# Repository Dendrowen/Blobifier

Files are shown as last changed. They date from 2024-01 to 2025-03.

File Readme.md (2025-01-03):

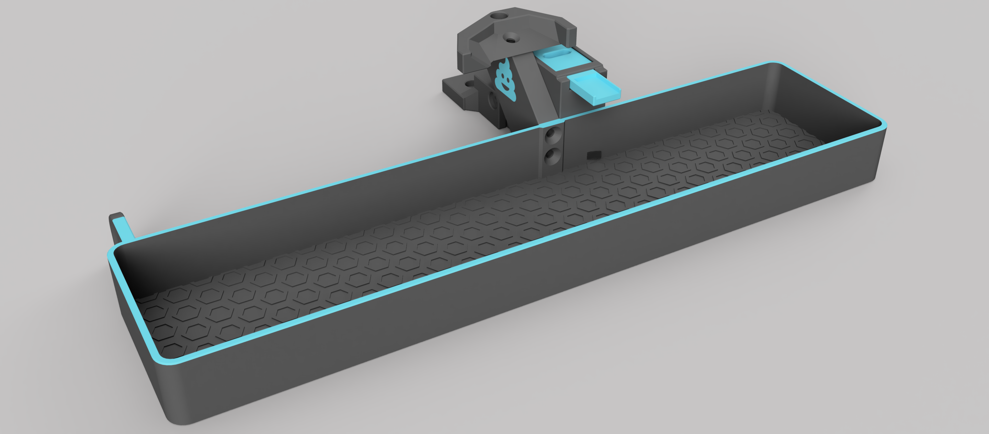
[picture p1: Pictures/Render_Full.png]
Blobifier Render

Do you like the Blobifier? Consider [buying me a coffee](https://www.buymeacoffee.com/dendrowen) or support me through [paypal](https://www.paypal.com/donate/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)

# 1. What is it?
The Blobifier is a small device that eliminates the need for a purgeblock, making filament swaps more quick. It does this by extruding filament onto a tray creating a blob that will get ejected into a purge-bucket.
## 1.1 Features
- Turn your filament purge waste into blobs for fewer waste and quicker purging.
- Store the blobs in a bucket that can hold **400 blobs!** (for the V2 300mm version)
- Automatically pause the printer once the bucket is full.
- Detect when the bucket is installed or missing.
    - NOTE: Empty the bucket if you remove it! The system will reset the blob counter.
- Shake the bucket for better dispersion of the blobs in the bucket.
- Clean your nozzle on a brass brush before resuming to print.

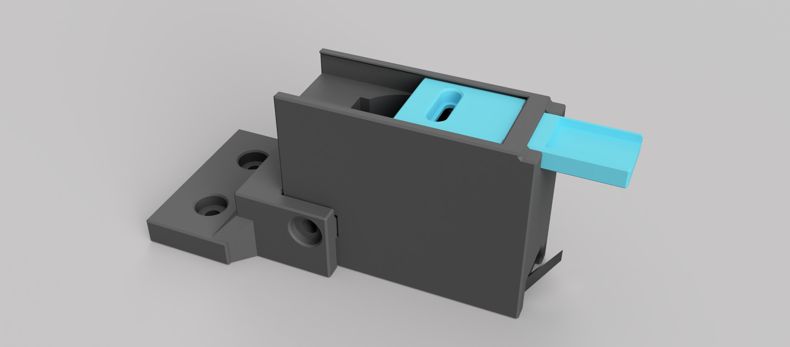
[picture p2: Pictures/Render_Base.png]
Blobifier Render


Blobifier Video (https://www.youtube.com/watch?v=VNMafOdnZ84) Blobifier Video (https://www.youtube.com/watch?v=a73EYLjRkbQ)

# 2. Credit where credit is due
The Macro and Nozzle Scrubber are based on a version madde by by Hernsl (hernsl#8860 on Discord). 

# 3. Who is it for?
The device is designed around a Voron V2.4 300mm, but should work for 250mm and 350mm too. This version only supports the assembly on the rear-left of the bed. If you decide to change all this, please consider contributing to the project by creating a pull request with the needed changes.

# 4. BOM
Complete kit at:
- [aliexpress - Seleadlab](https://s.click.aliexpress.com/e/_DCsTsHL)
- [aliexpress - Fysect](https://s.click.aliexpress.com/e/_opb6U3d)
    - Requires other .stl files. Linked in the product description!
- .stl files should be printed using default Voron settings
  
Parts:
- 3 x M3x8 shsc
- 1 x M3x25 shsc
- 3 x M3x8 fhcs
- 3 x M3 t-nut
- 1 x M2x6 shsc (For the servo pivot arm)
- 2 x M2x10 self tapping screws
- 5 x heat set inserts
- 1 x 10x30 aluminum strip
    - max 1mm thick
    - Make sure it's thick enough to dissipate the heat from the nozzle
    - If you have the 'old' 10x15 strip, print the proper tray to match it.
- 1 x SG90 or MG90 servo (and the included screws)
- 1 x omron D2F-5L sized micro switch. Any knock-off will work.
- 1 x brass brush
- 1 x 4-pin jst connector set (male + female)
- other connectors and wire to connect it to the board

# 5. Build instructions
## 5.1 Bucket
### 5.1.1 Printed Parts
- **Bucket_*.stl** (whichever suits your printer (and printbed))
- **\*_Shaker.stl** (whichever suits your toolhead)
- **\*_Shaker_Arm.stl** (whichever suits your toolhead)
    - The included **\*_Shaker_arm_poo.stl** can be used for a multimaterial print.
### 5.1.2 Assembly
1. Insert 4 heatset inserts in the arm. Mind that one needs to be inserted at an angle.
2. Screw the arm to the bucket with the *poo* being upright using 2 M3x8 fhcs screws.
3. Screw the shaker to the arm with the opening facing the bucket using an M3x8 fhcs and M3x8 shsc screw.

## 5.2 Brush
### 5.2.1 Printed Parts
- **Brush.stl**
### 5.2.2 Assembly
1. Cut off the handle from the brass brush and insert it into the printed part. If it doesn't fit smootly, file down the brush further until it does.
2. Screw the brush down on the left bed extrusion with the brush against the rear of the bed using an M3x8 shcs and t-nut.

## 5.3 Base
### 5.3.1 Printed Parts 
- **Base.stl**
- **Tray.stl**
- **Servo_arm_*.stl** (Check which arm fits properly on your servo)
- **Mount_*.stl** Check the mount for your printer. The V2.4 has two mounts because some beds are slightly wider(255, 305 or 355)
- **Base_shim.stl** The tray needs to be sligtly above the bed surface (Scale Z height of the object according to your needs. Keep in mind that the higher this part is, the longer the mounting screws need to be)
### 5.3.2 Assembly
1. Glue the piece of aluminum inside the tray. It might require a little force to make it slide into the cavity. Make sure the piece of aluminum is thick enough to dissipate heat from the nozzle without melting the plastic.
1. Sand down the tray untill the top and bottom are smooth. If the aluminum pertrudes the top a bit, sand that down with it.
1. Remove 3 included support from the base.
    - One in the slot for the tray
    - Two at the bottom for the switch and jst connector
1. Test fit the tray in the base. Slide it in from the back. It should stick out 15mm if fully inserted. If operation isn't smooth, go back to step 2.
1. Remove the tray from the base
1. Insert the servo from above making sure the wires face the cavity meant for them and are inserted first so they come out from the bottom. It could be a tight fit, but if your printer is properly tuned you shouldn't have any trouble. Make sure you inserted it fully, you can check from the bottom.
1. Insert the microswitch in the bottom. Check if the lever is correctly oriented. Screw it down with 2 M2x10 self tapping screws. The screw holes might be hard to see, because there is an extra layer for printability.
1. Insert the 4-pin female JST connector iside the slot. If the fit is very loose, use some glue. 
1. Solder the wires from the servo and the switch to this connector. The order is less important, just keep in mind that you'll have to connect the wire to the board in the same order.
    - pin 1: VCC (Red, usually)
    - pin 2: 
        - GND from the servo (Brown, usually)
        - C from the switch (pins are marked C, NC and NO)
    - pin 3: Signal wire from servo (Orange, usually)
    - pin 4: NC from the switch
1. Connect the base to your printer with a cable of your own making. You can drill a hole in the bottom plate of your printer to feed the wire through. **Be careful not to hit any components in your electronics compartment and ALWAYS unplug your printer from the wall if you're working on the electronics!** You'll have to pick empty pins on your board. Refer to your boards documentation on which pins to use.
    - pin 1: 5V (any 5V on your board should work)
    - pin 2: GND (any GND on your board should work)
    - pin 3: An output capable pin. Most of them are.
    - pin 4: A pin with an internal pullup resistor. Most of them have.
1. Insert a heated insert into the base mount. Only one side is suitable for it.
1. Slide the base in the mount and secure it with an M3x25 shsc.
1. Screw the base into place with 2 x M3x8 shcs and T-nuts onto the left 2020 extrusion. The tray should just slide behind your bed. You can temporarily insert the tray to verify the position.
1. Turn on your printer and include the config file found in the github. Then restart the klipper firmware.
1. run `BLOBIFIER_SERVO POS=out` in the console. You should hear your servo move.
1. Screw the servo arm onto the servo with the arm pointing towards the slot. Make sure you don't turn the servo while doing this. If you accidentally turn it, run `BLOBIFIER_SERVO POS=out` again and continue.
1. Insert the tray from the back until the hole in the servo arm becomes visible through the tray. Then screw it down with an M2x4 screw, then go back half a turn so the screw can rotate freely in the tray.
1. Test the servo a couple of times with `BLOBIFIER_SERVO POS=in` and `BLOBIFIER_SERVO POS=out`. The tray should be fully inside or outside the base. If not, try to determine why.
    - There may be too much resistance in the sliding mechanism.
    - You might have screwed the m2 screw too tight.
    - The values in the config might need adjustment (unlikely)
1. Push the switch on the base. A message that the bucket is placed should be on the screen. Then let go of the switch. A message that the bucket was removed should be on the screen.
1. Place the bucket and see if it still works. If not, the base might need slight adjustment towards the center.

# 6. Configuration
Refer to the config files comments to configure the macro to your desires.

For maximum integration with Happy Hare, make use of the [gcode pre-processing](https://github.com/moggieuk/Happy-Hare/wiki/Gcode-Preprocessing). Make sure to include `PURGE_VOLUMES=!purge_volumes!`

Add BLOBIFIER to the post_load sequence in mmu_macro_vars.cfg
`variable_user_post_load_extension   : "BLOBIFIER"`

That's it. The Blobifier will now automatically be called for a purge everytime you swap materials. Oh... don't forget to disable that filthy wipe tower.

# 7. Release notes
## version 1.5
- Purge with a pulsating (and occasionally, retracting) motion. This will prevent laminar flow from occuring and purge the old filament more quicly. (Up to 30% EXTRA filament saved!)
- Changed the blob calculation mode. The blob will now split into equal parts if it is too large (e.g. 2x85mm instead of 150mm + 20mm). This will eliminate/reduce the small blobs scattering over the buildplate.
- Due to the above changes, certain variables have been added and removed:
  - new:
    - `z_raise`: The total amount the nozzle should be raised during a blob. The value should be somewhere around `iteration_z_raise * max_iterations_per_blob - triangular(iteration) * iteration_z_change`
    - `z_raise_exp`: The rate at which the hotend reduces raising speed during a blob. `0.85` seems to be a good starting value.
    - `purge_length_maximum`: The maximum length of the entire purge. Use `max_iterations_per_blob * max_iteration_length`.
  - removed:
    - `iteration_z_raise`
    - `max_iterations_per_blob`
    - `iteration_z_change`
    - `max_iteration_length`
- Revised some parameter checks to work with the new Happy Hare version 2.7
- Add settings:
  - `shaker_arm_z` to allow for different bed/shaker arm heights.
  - `brush_accell` to be able to change the acceleration of the brush movement.
- Keep in mind I do not maintain the `SW Only Blobifier.cfg`
## version 1.4
- Add a safe descend mode. This makes sure the toolhead can get down to the tray without hitting your prints. (requires exlude objects enabled in your slicer)
- Change the tray to fit a 30x10x1mm aluminum strip. This will prevent the tray from sagging over time. (The old tray is still available for these that have the smaller aluminum piece)
## version 1.3
- Add BLOBIFIER_PARK for use in conjuntion with Happy Hare. Parking prevents oozing.
- Removed the retraction moves (apart from the initial one in BLOBIFIER_PARK)
- Add a dwell time to relieve pressure from the nozzle
## version 1.2
- Purge volumes are now extracted from the new Happy Hare tool map!
- It is now advised to use the 'variables' of Happy Hare branch in conjunction with this mod.
- Add support for wider beds (5mm extra width) ([#6](https://github.com/Dendrowen/Blobifier/issues/6))
- Persistent blob state! Values are saved across reboots
## version 1.1
- Now fits the MG90 servo too!
- Tray height reduced to accomodate for the MG90 servo.
- Base servo cavity expanded for fitting an MG90.
- Added a channel alongside the servo for wiring the microswitch.
- Improved servo arm and removed different fits.
- Included supports in the base for easier printing.
- Modified the macro so it temporarily restores the feedrate to 100%.
- Adjusted the part cooling options. You can now either set it to a desired speed, or don't change it at all.
- Added some simple validation in the config to prevent bad values for the parameters.
## version 1.0
- Designed from the ground up in Fusion 360.
- Changed the way the system mounts for easy adaptation.
- Hexagon pattern on the bucket floor! (For smoother distribution, and hexagons are bestagons).
- Change shaker shape to better fit the Stealthburner toolhead.
- Included supports in the mount and brim-ears for the bucket.
- Add chamfers to most edges.
## version 0.3
- Add the poo icon for multicolored prints.
- Add a shaker arm to the bucket which the SB can slide into.
    - Other toolheads may be added in future releases.
- Move the brush to the right.
- Increase bucket height to 23mm.
- Add ridges to the bucket floor to help spread the blobs.
- Add a micro switch to the base bottom to detect the bucket.
- Updated BOM to include hardware for the brush
- Increased the hight of the base by 0.2mm for more support to for the tray
## version 0.2 & 0.1
- I... started making release notes with version 0.3

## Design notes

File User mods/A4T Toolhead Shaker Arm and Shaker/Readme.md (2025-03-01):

# A4T Shaker Arm Mod

A modified version of the shaker arm and shaker to fit the A4T toolhead.

CAD

## Variations Against the Stealth Burner Shaker Design

1. One M3x8 SHCS screw is needed to mount the shaker on the shaker arm.  
2. The shaker and shaker arm have indentations to align themselves to each other and prevent the shaker from twisting on the shaker arm, removing the need for the second M3 screw.  
3. The shaker and shaker arm have been made slimmer in the X direction to ease clearance between the front left Z belt and the shaker when inserting and removing the bucket from the printer.

## Bill of Materials (BOM)

### Printed Parts
- **Bucket_*.stl** (whichever suits your printer and print bed) – same as the Blobifier STL’s folder  
- **Shaker_A4T.stl**  
- **Shaker_Arm_A4T.stl**
Print using standard Voron part settings

### Hardware
- Same as the Blobifier. You won’t need the third M3x8 FHCS screw.



## Assembly

1. **Insert 3x M3 heat set inserts** in the shaker arm. Use an exacto knife or metal object to “level” the heat sets with the part, ensuring the inserts are flush with the surface of the arm and no excess material is oozing out.  
2. **Mount the arm to the bucket** (with the poo logo upright) using 2x M3x8 FHCS screws.  
3. **Align the shaker notches** to the arm and secure with the M3x8 SHCS screw.



## Calibration

Install and calibrate your shaker Z height as per the Happy Hare instructions.

- In a Voron 350, you might set `variable_shaker_arm_z` to `2mm`.  
- If the A4T is rubbing against the bottom of the shaker, increase slightly to `2.5mm` or `3mm`.  

## Video

Watch the video (https://youtube.com/shorts/eVDUzT1yRBc)

Happy printing!

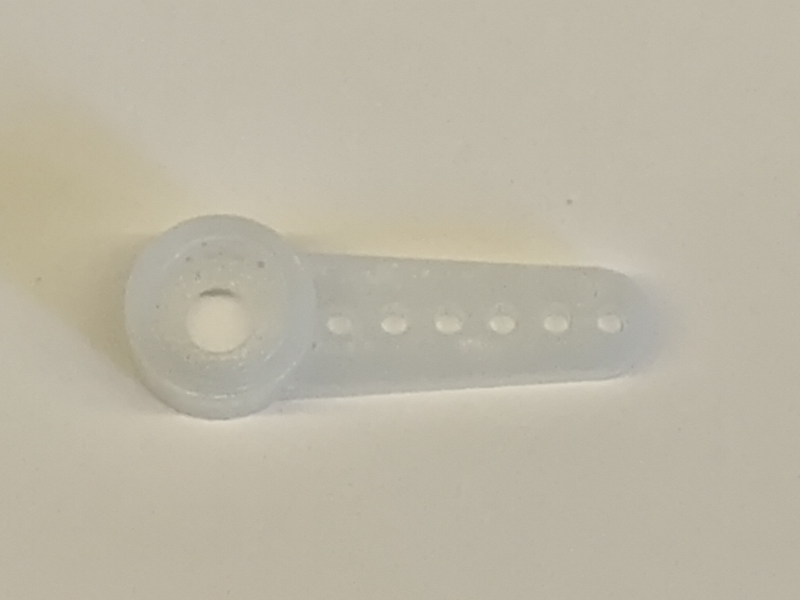
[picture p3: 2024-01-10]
Pictures/servo arm.jpg

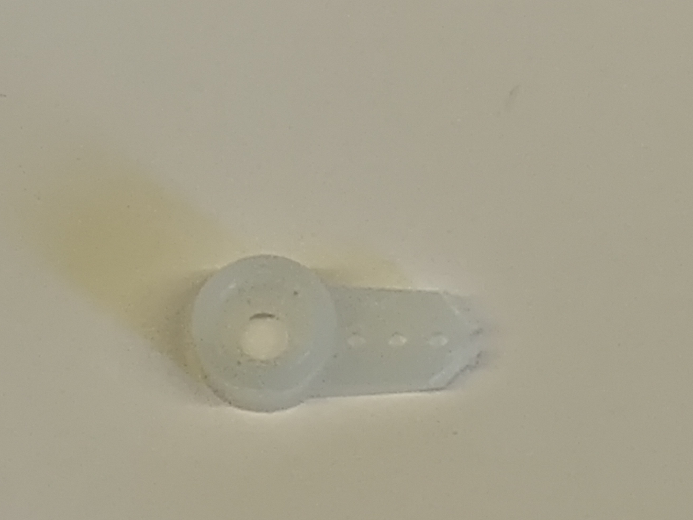
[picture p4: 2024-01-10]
Pictures/servo arm cut.jpg

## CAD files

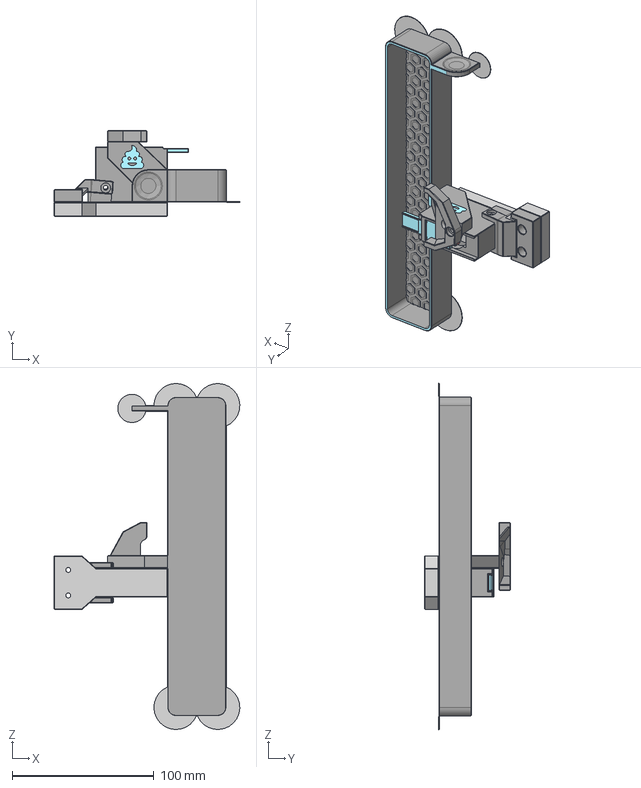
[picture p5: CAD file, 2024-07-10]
Source files/Blobifier.step
131.1 x 60.5 x 244.2 mm
Tray
Base
Mount_voron_2.4
Bucket
Shaker
Arm
[a]_servo_arm_MG90S-3PS v2
Base shim

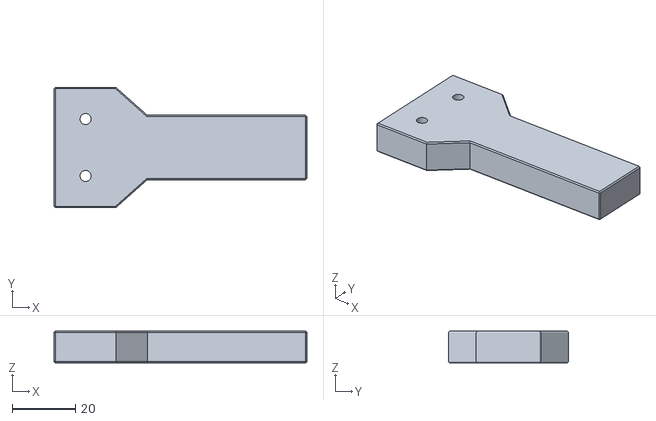
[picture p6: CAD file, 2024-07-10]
STLs/Base/Base_shim.stl
80.0 x 38.0 x 10.0

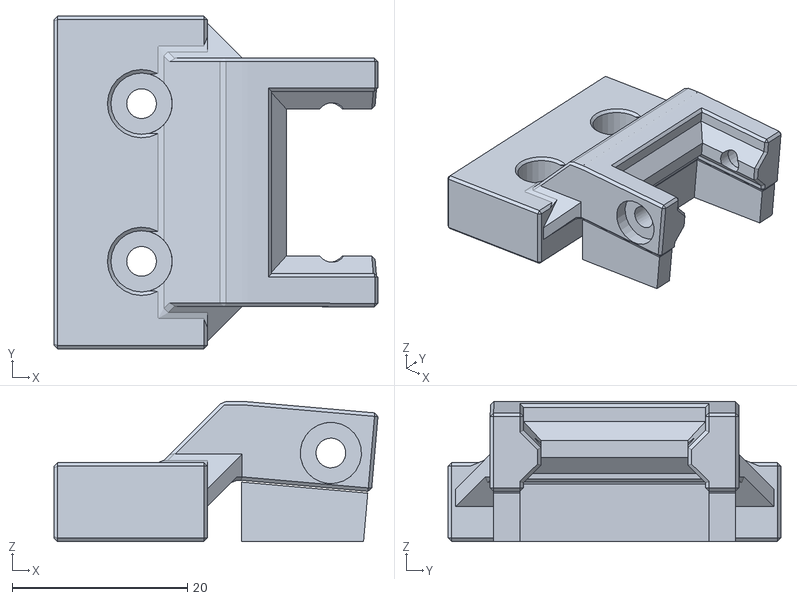
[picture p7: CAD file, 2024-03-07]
STLs/Base_mount/Mount_voron_2.4_10mm_wider_beds.stl
37.0 x 38.0 x 16.0

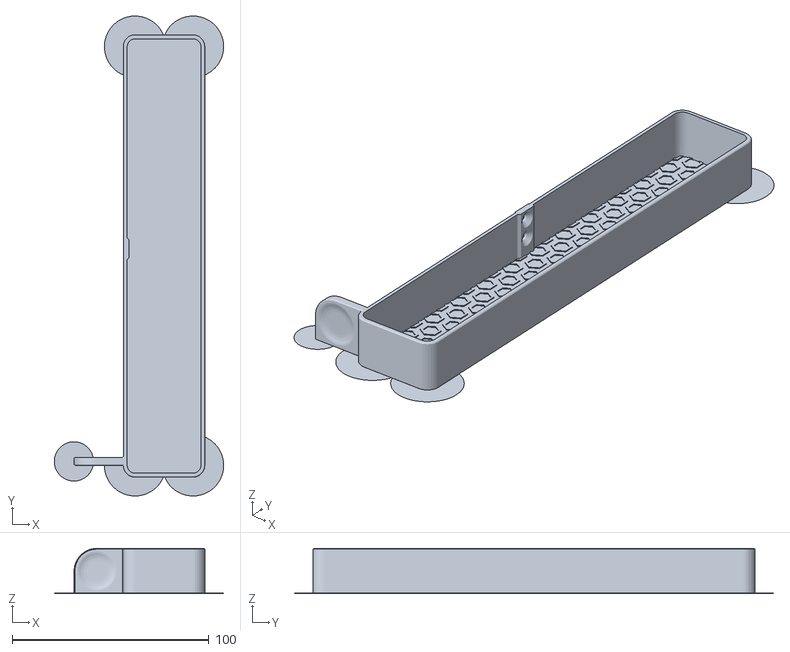
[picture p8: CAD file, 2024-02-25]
STLs/Bucket/Bucket_V2.4-255.stl
86.2 x 244.2 x 23.0

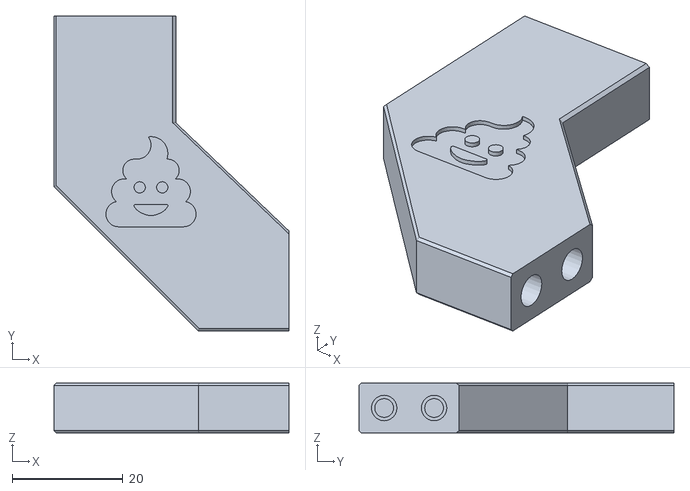
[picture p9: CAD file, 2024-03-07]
STLs/Shaker_arm/Kirigami_bed/SB_shaker_arm.stl
42.4 x 56.7 x 9.00

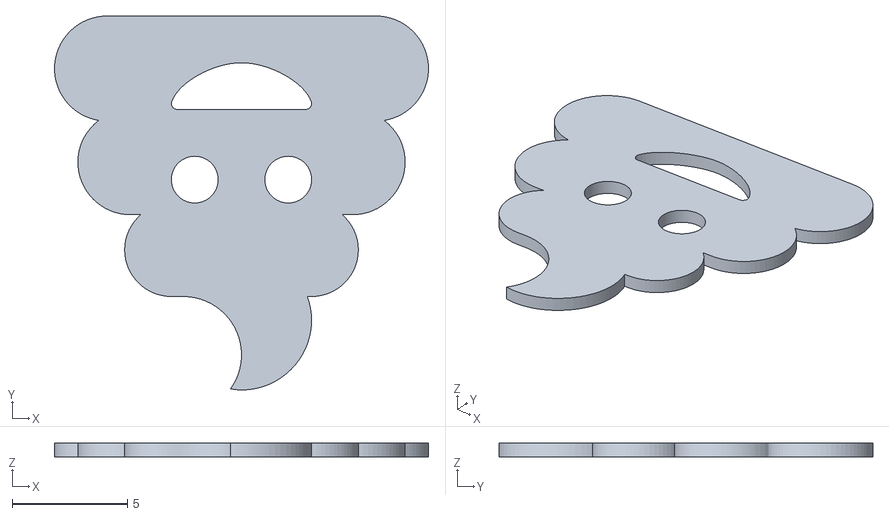
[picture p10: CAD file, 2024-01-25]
STLs/Shaker_arm/Regular/SB_Shaker_arm_poo.stl
16.3 x 16.3 x 0.6

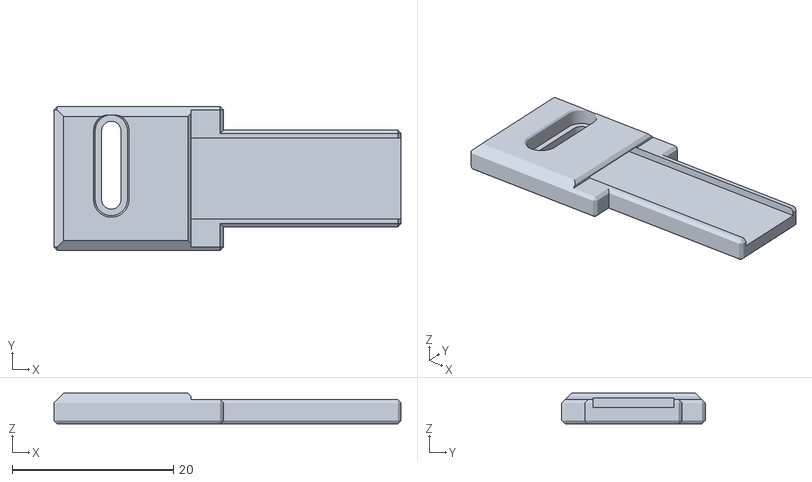
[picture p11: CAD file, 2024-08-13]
STLs/Tray.stl
43.0 x 17.8 x 3.80

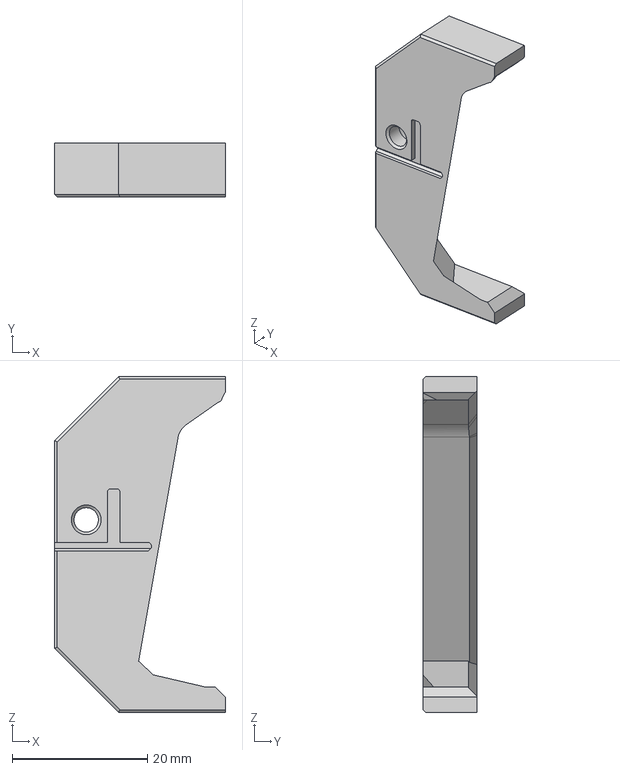
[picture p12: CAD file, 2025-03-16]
User mods/A4T Toolhead Shaker Arm and Shaker/CAD/Shaker_A4T.step
25.3 x 8.00 x 49.7 mm

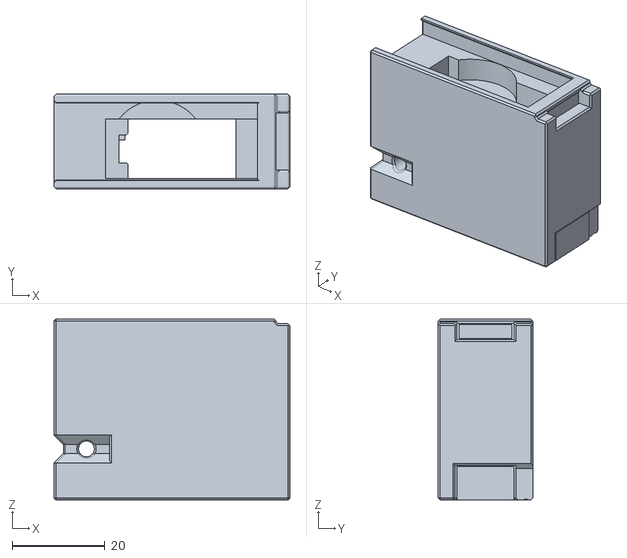
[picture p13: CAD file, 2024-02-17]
STLs/Base/Base.stl
50.9 x 20.4 x 39.0

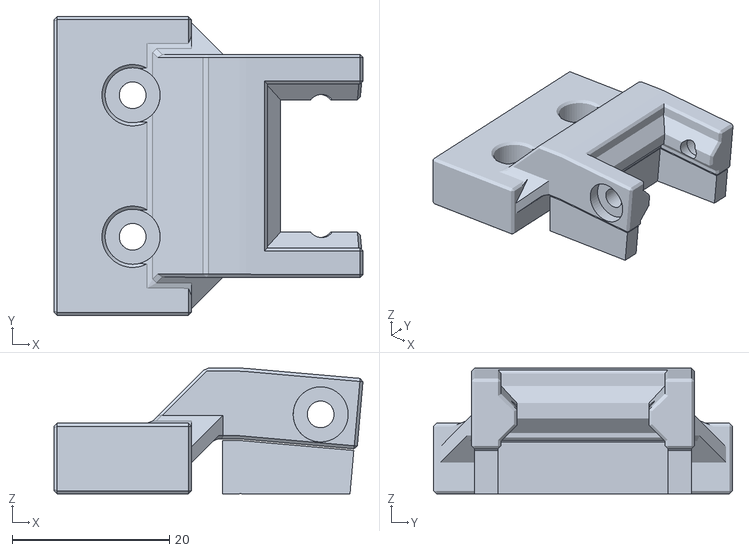
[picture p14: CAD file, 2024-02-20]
STLs/Base_mount/Mount_voron_2.4_5mm_wider_beds.stl
39.3 x 38.0 x 16.0

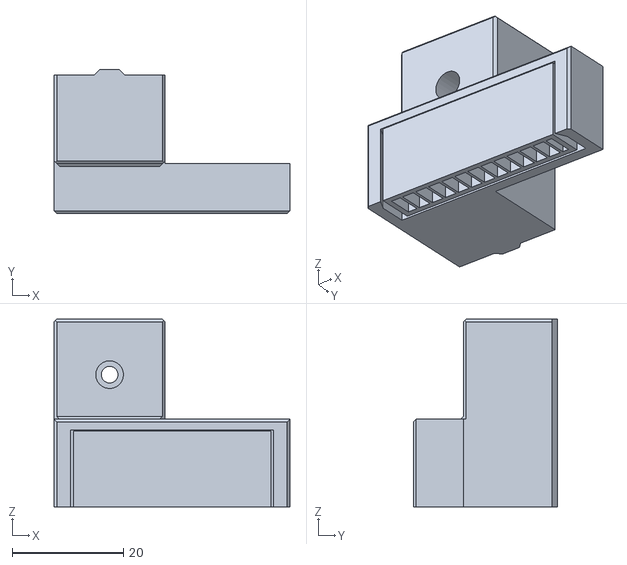
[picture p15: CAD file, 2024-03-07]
STLs/Brush_high_beds.stl
42.5 x 26.0 x 33.8

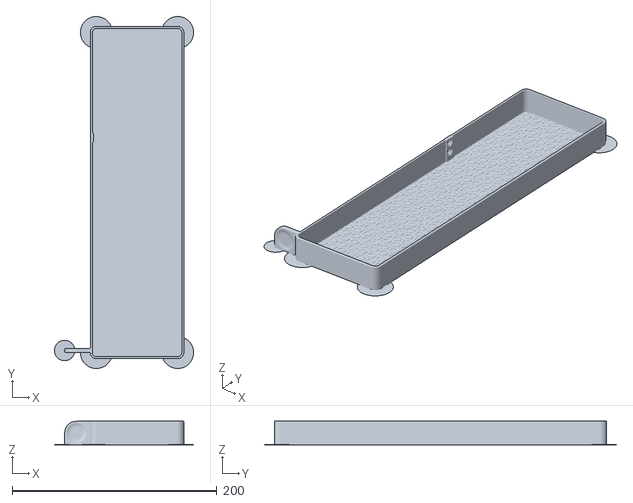
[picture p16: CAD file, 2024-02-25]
STLs/Bucket/Bucket_V2.4-355.stl
136.2 x 344.2 x 23.0

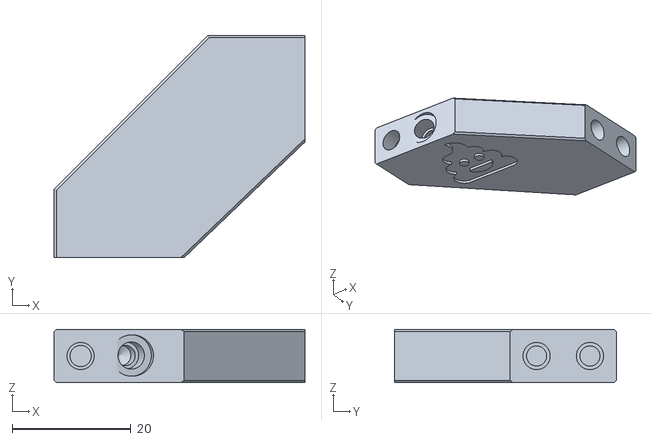
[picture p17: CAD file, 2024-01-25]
STLs/Shaker_arm/Regular/SB_Shaker_arm.stl
42.4 x 37.5 x 9.00

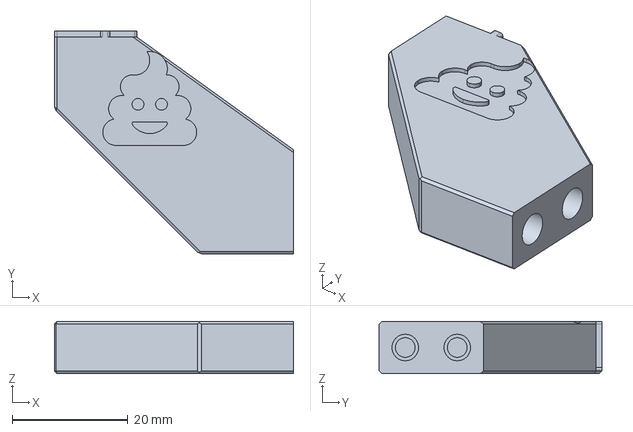
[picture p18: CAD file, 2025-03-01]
User mods/A4T Toolhead Shaker Arm and Shaker/CAD/Shaker_Arm_A4T.step
41.4 x 38.5 x 9.00 mm

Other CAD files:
STLs/Base_mount/Mount_voron_2.4.stl
STLs/Bucket/Bucket_V2.4-305.stl
STLs/Servo_Arm.stl
STLs/Bucket/Bucket_V2.4-300.stl
STLs/Brush.stl
STLs/Bucket/Bucket_V2.4-250.stl
STLs/Bucket/Bucket_V2.4-350.stl
STLs/SB_Shaker.stl
STLs/Tray_old_shorter_aluminum.stl
User mods/A4T Toolhead Shaker Arm and Shaker/STL/Shaker_A4T.stl
User mods/A4T Toolhead Shaker Arm and Shaker/STL/Shaker_Arm_A4T.stl

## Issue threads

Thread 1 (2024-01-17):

change

booom691, 2024-01-17:
nice project, but I recommend a change

Mount it on the back of the profile and rotate the servo so that it is on top. This way, the nozzle can be cleaned without having to change the height of the Z-axis (Voron 2.4). Print it in two parts to adjust the nozzle height, similar to the Klicky probe

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

Dendrowen, 2024-01-18:
In that case the brush and bucket would also need gantry mounting, which is getting a bit much. The bucket would then als need to be a lot smaller which defeats the purpose for this device. Thanks for your input though!

Closed 2024-01-18.

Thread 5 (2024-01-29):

Servo_arm_???.stl

evelyndooley, 2024-01-29:
Wondering where these files are. They're mentioned in the README but don't seem to appear in the repo. May have forgotten a `git add` ;)

Dendrowen, 2024-01-29:
Oh, your absolutely right! I'll add them. I didn't think of it anymore because I'm using the provided servo arm.

ksteddom, 2024-09-11:
I'm having trouble getting the Servo_Arm.stl to fit a MG90S servo. It sticks up too high and interferes with the tray sliding. I have verified that the servo is completely seated in the slot and the arm is pressed all the way down. @Dendrowen do you mean to say you are using one of the servo arms that comes with the servo or the newer Servo_Arm.stl file?

Dendrowen, 2024-09-12:
I'm using the included servo arm atm. That one seems to work fine for me. Did you print it in the provided orientation?

ksteddom, 2024-09-12:
Thanks for the clarification. I thought I printed it correctly. I’m going to print it again to double check. If I have any more issues  I’ll start a new thread.

Closed 2024-01-29.

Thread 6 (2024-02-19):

Problem with base on Formbot v2 350 - Bed is higher

AMFkuna, 2024-02-19:
I have a problem with the base on my 350. Even if I move the bed as far to the right as possible, it still interferes with proper bed placement.

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

AMFkuna, 2024-02-19:
I had to cut off the base to make it fit.
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

Dendrowen, 2024-02-19:
What is the width of your bed?

AMFkuna, 2024-02-19:
355

Dendrowen, 2024-02-20:
I have added a new mount for the slightly wider beds. (My bed is 300mm)
This should solve the 2.5mm misalignment. You can find it in the beta branch. Do you want to test this and report back?

AMFkuna, 2024-02-20:
Mount does not solve this, it also shifts the bucket switch and creates a gap between bucket and base.

Dendrowen, 2024-02-20:
Oh, right. In that case I'll leave this open for now while I'll think of a pretty solution

Dendrowen, 2024-02-25:
Included wider buckets

Closed 2024-02-25.

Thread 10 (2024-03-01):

kinematic mounts

jckennell, 2024-03-01:
for the bases for the people with kinematic bed mounts, there are 2 poplular sets that people use. the mounts from Mandela Roseworks sits the bed higher than the whoppingpochard kinematic mounts. i modified mine to 55.4mm tall (16.7mm taller than the original base). also the shaker arm needs to be 16.7mm taller for beds that sit higher, as well as the nozzle brush.
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

Dendrowen, 2024-03-05:
Thanks! Did you create this in the .step or .f3z files?

jckennell, 2024-03-05:
I used your .step file. My Fusion skills aren't very good, but basically just added a block on top of the arm and and put the holes in it. I should have saved it, but I didn't because I'm using Fusions free hobby license, which only let's me save so many files. So the ones that get deleted are the most simple ones to recreate if I have to. I just posted the Pic for reference as to what I did for that part.Sent from my T-Mobile 5G Device
-------- Original message --------From: Sjon Huisman ***@***.***> Date: 3/5/24  12:20 PM  (GMT-05:00) To: Dendrowen/Blobifier ***@***.***> Cc: jckennell ***@***.***>, Manual ***@***.***> Subject: Re: [Dendrowen/Blobifier] kinematic mounts (Issue #10)
Thanks! Did you create this in the .step or .f3z files?

—Reply to this email directly, view it on GitHub, or unsubscribe.You are receiving this because you are subscribed to this thread.Message ID: ***@***.***>

Dendrowen, 2024-03-07:
Makes sense. Do you still have the .STL, and if so. could you create a pull request or send it to me on Discord?

jckennell, 2024-03-07:
I messaged you on the discord. Github is witchcraft to me. I've tried adding files, pull requests, branches, forks. It's all beyond me. LolSent from my T-Mobile 5G Device
-------- Original message --------From: Dendrowen ***@***.***> Date: 3/7/24  6:49 AM  (GMT-05:00) To: Dendrowen/Blobifier ***@***.***> Cc: jckennell ***@***.***>, Manual ***@***.***> Subject: Re: [Dendrowen/Blobifier] kinematic mounts (Issue #10)
Makes sense. Do you still have the .STL, and if so. could you create a pull request or send it to me on Discord?

—Reply to this email directly, view it on GitHub, or unsubscribe.You are receiving this because you are subscribed to this thread.Message ID: ***@***.***>

Dendrowen, 2024-03-07:
Files are added. Thank you very much!

Closed 2024-03-07.

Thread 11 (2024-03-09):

.step does not include tray part

53Aries, 2024-03-09:
Just fyi. Thanks.

Garr-Garr, 2024-05-01:
It looks like it's included:

> https://github.com/Dendrowen/Blobifier/blob/main/Source%20files/Blobifier.step

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

53Aries, 2024-07-02:
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

I don't see it. By tray im referring to blob tray connected to the servo.
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

Closed 2024-07-10.

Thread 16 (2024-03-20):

Missing support: Base+3.stl and Base+4.stl

Anollya, 2024-03-20:
Missing support: Base+3.stl and Base+4.stl

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

Dendrowen, 2024-07-10:
I'm planning to add a more robust way to add different heights, but it'll be a while

Closed 2024-07-10.

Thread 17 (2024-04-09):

Blobifier start position Z height issue

PaulMellor, 2024-04-09:
Whilst testing the Blobifier I found that with a beacon, it does not account for the brush height when moving from z homing position to the brush start position causing it to short out the Beacon terminals, as keeps everything at the same height and just moves the xy.
Can we make it check the current Z height and ensure it is above the Brush height plus 2mm. to ensure it does not cause a short or avoidable collision with objects.
I am assuming it is not an issue with printing as assume it would do a z hop before moving. I haven't gotten to this part of testing still tuning things.

Dendrowen, 2024-07-10:
I'm reluctant on adding too many alterations to accommodate other mods. You could overwrite the macro in and make sure it's above the brush and then calling the original

Closed 2024-07-10.

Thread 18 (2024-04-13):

Gantry mount

Maximus2711, 2024-04-13:
It seems like ultimate solution for purging, like collaboration blobifier and eap project.

Dendrowen, 2024-05-13:
Not possible due to the needed z travel relative to the blobifier base. Sorry.

baracoder, 2024-10-03:
:thinking: Maybe it could work. Here is my idea: The base is mounted at an angle and instead of Z, the toolhead can move in X or Y direction while extruding away from it. What do you think?

Dendrowen, 2024-10-09:
I say, go ahead and try. I think there are better solutions for this but the Blobifier isn't really designed for that.

Closed 2024-05-13.

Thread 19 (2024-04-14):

Servo return in neutral position when not ussed after "in" command

kktonev, 2024-04-14:
It looks like this line makes servo to turn in neutral (middle) position:
SET_SERVO SERVO=blobifier WIDTH=0

I try almo any other settings - no change.
Also I try different servos - no change.
After this line is executed almost any 1 of 5 execution of "BLOBIFIER_SERVO POS=in"
leads to non-requried movement of the servo.

Its very likely to be seen when set higher value for "variable_dwell_time:".
I make it 1200. Its clearly hearable when the servo is turned off.
So it turns in neutral with more delay if the value is bigger, but there is no change in this behaiveier.

UPDATE:
I comment out the line:
SET_SERVO SERVO=blobifier WIDTH=0

I think is not a problem, because I use external 5V supply for all the servos.

Seleadlab, 2024-06-06:
Set the variable_dwell_time in gcode_macro BLOBIFIER_SERVO to 0

Closed 2024-07-10.

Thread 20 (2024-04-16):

I encountered a fan error while using blobifier.

fqscfqj, 2024-04-16:
Error evaluating 'gcode_macro BLOBIFIER:gcode': jinja2.exceptions.UndefinedError: 'extras.gcode_macro.GetStatusWrapper object' has no attribute 'fan'
Is it related to OrcaSlicer? The cooling fan is set to fan0.
There was no error when I deleted the blobifier configuration from ercf.
Here is my configuration.
[config.zip](https://github.com/Dendrowen/Blobifier/files/14986207/config.zip)

fqscfqj, 2024-04-17:
When I changed [fan_generic fan0] to [fan], the error disappeared. How should I use OrcaSlicer and blobifier at the same time?
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

fqscfqj, 2024-04-18:
Alright, just need to comment out all the conditions.
#  {% if part_cooling_fan >= 0 %}
#    {% set backup_fan_speed = printer.fan.speed %}
    M106 S255 #{part_cooling_fan * 255}
#  {% endif %}

fqscfqj, 2024-04-18:
Alright, just need to comment out all the conditions and only keep one M106 S255.

Closed 2024-04-26.

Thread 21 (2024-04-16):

Slot support fused in Base+1

Mordenkainen, 2024-04-16:
It appears the slot support is a fused to the base in Base+1.stl.

The others all seem ok, but Base+1 appears fused and even looking at the unsliced STL in the slicer has a visibly different support structure.

Dendrowen, 2024-07-10:
I'll add a more robust way to alter the height in the future, but it'll be a while. Sorry

Closed 2024-07-10.

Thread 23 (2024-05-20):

Fusion file has a lost sketch plane issue

jwhite, 2024-05-20:
Sketch plane was lost here:
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

Likely this was done when the work was done to create different bed widths.

Dendrowen, 2024-07-10:
yeah. I'm quite the F360 beginner. No clue on how to fix this.

Closed 2024-08-21.

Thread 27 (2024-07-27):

Sovol Sv08

checkitog, 2024-07-27:
Hi friend, I have a sovol sv08 with ercf, could blobifier be adapted for this machine?

Dendrowen, 2024-08-21:
I believe spoke to you on discord? It probably can, but I don't have one to test it and find it a bit unnecessary.

checkitog, 2024-08-27:
I made my own design for the purges, and my own bucket, it is a design without servo, but I can't get the macro to respond the way I need it to.

Closed 2024-08-21.

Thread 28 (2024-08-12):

Blobifier without the Extras?

Durahl, 2024-08-12:
Is it possible to run Blobifier without the rest like the Purge Bucket getting shaken, the activation of a Servo, etc...?

If so, how could one accomplish this?

Dendrowen, 2024-08-21:
There is a SW only blobifier.cfg file in the repo that uses the bed for blobbing and knocks it off using the toolhead. The shaking can be disabled in the default version with `variable_bucket_shake_frequency: 0`

Durahl, 2024-08-25:
Uhm... Is the `SW only Blobifier.cfg` a Standalone thing or does it work in combination with parts of the HH Setup? 🤨

My understanding after reading through `SW only Blobifier.cfg` is that while I **_am_** able to define the **X-Axis** location of where to start Brushing and to stop via `variable_brush_start` and `variable_brush_width` there doesn't seem to be a Setting for where on the **Y-Axis** this is supposed to happen.

Same for where to do the Purge... There is again only a `variable_purge_X` but no `variable_purge_Y`.

Dendrowen, 2024-09-10:
I'd ask this question in the ercf_questions discord channel. The developer of the SW only roams there.

Closed 2024-08-21.

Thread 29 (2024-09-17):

Base without supports

alidaf, 2024-09-17:
I've printed 3 bases so far but trying to remove the support in the tray slot leads to something being broken. Could you provide a version without the built-in supports.

Dendrowen, 2024-10-09:
You should be able to split the design in the slicer and remove the supports.

Closed 2024-10-09.

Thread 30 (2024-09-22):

Feature Request: Add small lift to park macro when tray is higher than bed.

rykerg9, 2024-09-22:
I've had to manually add a G1 command to lift the toolhead so that it doesn't crash into the tray during the first few layers of a print. See below for my kind of jank fix. 2nd G1 command is the one I added.

```
[gcode_macro BLOBIFIER_PARK]

    ...

G1 X{bl.brush_start} Y{position_y} F{bl.travel_spd_xy}

G1 Z{bl.tray_top + 5} F{bl.travel_spd_z}

G1 X{bl.purge_x}

    ...
```

Dendrowen, 2024-10-09:
I've added a variable for the shaker arm height which should prevent this if set correctly. The update should come with the next Happy Hare update somewhere this week. Please feel free to reopen if it didn't work

rykerg9, 2024-10-30:
Sorry for the delay in response- it's been a crazy month for me.
I believe there has been a misunderstanding in regards to what exactly the issue was. I was having trouble with the nozzle not being lifted during the first few layers when swapping filaments, causing the nozzle to collide with the purge tray. For clarity, it would be ideal if a variable or macro could be integrated to lift the nozzle above the tray height when it is below said height before moving over to the tray.

Apologies for the confusion.

Closed 2024-10-09.

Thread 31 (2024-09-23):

Need Base shims for alternate bed size mounts

kwalters3, 2024-09-23:
There needs to be alternate versions of Base_shim.stl to go along with the mount stls for the +5 and +10 bed sizes

Dendrowen, 2024-10-09:
Scale the shim in the z-direction to accommodate every height!

Closed 2024-10-09.

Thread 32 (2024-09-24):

Filament stays in hotend when bucket is full.

tdchaos, 2024-09-24:
When the bucker gets full the toolhead parks without retracting the filament. Then the print is paused, leaving the filament to cook and clog.

Filament ahould get cut or tip formed before pausing.

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

Dendrowen, 2024-10-09:
Doesn't your idle_timeout turn off your hotend preventing this?

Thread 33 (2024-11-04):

Issues with probing.

Zchulski, 2024-11-04:
The shaker arms is too big for the Voron tap, at least for mine.  the X axis parts hit the shaker arm and throw off tap when probing the bed

Dendrowen, 2024-11-09:
I had no issues with voron Tap on this, but changing the QGL locations more inward might help. I don't really have any other solution because the arm needs to be able to reach the toolhead.

Closed 2024-12-29.

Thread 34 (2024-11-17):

Xol Toolhead Mantis Xol 2

jjrricardo, 2024-11-17:
Does it work with the Xol Toolhead Mantis Xol 2?

Dendrowen, 2024-12-22:
This is not an issue and will be closed. For support I refer you to the discord server: https://discord.gg/HXEHUb9W

Closed 2024-12-22.

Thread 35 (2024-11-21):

Default purge volumes

Zchulski, 2024-11-21:
Despite changing my default purge volume.  Blobifier still wants to purge about 400MM of filament on the first load.

Dendrowen, 2024-12-22:
If you have a purge map enabled/loaded, it reads from there. If the previous tool is unknown, it will take the largest value for that specific tool.

Closed 2024-12-22.

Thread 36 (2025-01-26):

Adjustable setting for Fan

JNSmith1717, 2025-01-26:
I have a cpap, and if I use the fan it deforms/cools blob way to quick. Could there betting a setting for fan speed when you use the fan?

ningpj, 2025-01-26:
You control the speed of the part cooling fan using the variable_part_cooling_fan setting.  -1 leave as set or 0..1.0 to set a specific speed for blobbing e.g 0.2 for 20%, 0 for off, 1.0 for 100%

JNSmith1717, 2025-01-26:
Ok made myself look stupid, haha. I guess I just wasn't reading/contemplating the verbage of it.

ningpj, 2025-01-26:
No worries.   Easily overlooked.
Please close the issue when you get a moment

Closed 2025-03-01.

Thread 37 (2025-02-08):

Hexagon pattern on 350mm bucket doesn't continue to end

ieRev, 2025-02-08:
Hi,

Just noticed the hexagon pattern on the bottom of the 350mm bucket stops short of the edge. It's fine on the the other sizes

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

Dendrowen, 2025-03-01:
Yeah, I was pretty much a novice in F360 when designing this and it just wouldn't cooperate. Adjusting this would take a significant amount of rework not worth it imo.

Closed 2025-03-01.

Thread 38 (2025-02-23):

Tuning/troubleshooting  guide

krzyzankowskig, 2025-02-23:
Hey,
There is a lot of good info in config files, but I still struggle to connect issues I have with basic settings for blobifier. For example I tuned tray height using paper method and I was almost alwayshaving blob that I stead of stay where it should was bending and sticking to the side of nozzle. I tuned it -0.01mm and suddenly it works fine. However today I was switching from pla to abs (which generated giant blob) and I saw so e struggle again...

So I wanted to ask if there is any kind of tunning / troubleshooting guide oth there? Or maybe so do e could share some basic tricks like if you have behaviour x play with parameter y? I will appreciate any help as I really like this system but still don't feel safe enough to run long unattended color prints :(((

Dendrowen, 2025-02-23:
For support I kindly refer you to the discord

https://discord.gg/yxCCuYNF

Closed 2025-02-23.

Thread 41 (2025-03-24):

Brush_high_beds.stl metric screw sizing wrong

drewgwallace, 2025-03-24:
The size for the M3 nut on Brush_high_beds.stl is too small. When comparing to Brush.stl it appears that original model was correct for a M3 SHCS.

I attempted to fix this in the CAD source files, but did not find the brush model.

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

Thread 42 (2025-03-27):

blobifier config

weismantelf, 2025-03-27:
Hello,

where can I find the blobifier config file for defining the pins for the servo and the switch?

thx

Frank

ningpj, 2025-03-27:
mmu/addons/blobifier_hw.cfg

Closed 2025-03-27.

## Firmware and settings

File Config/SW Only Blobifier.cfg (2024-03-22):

##########################################################################################
# THIS CONFIG FILE IS FOR USE WITHOUT THE ACTUAL BLOBIFER! 
#
# FOR THE 'CORRECT' VERSION, PLEASE USE HAPPY HARE, OR DOWNLOAD THE CONFIG FILE FROM THERE
##########################################################################################
# Main macro. Usually you should only need to call this one or place it in the Happy Hare
# _MMU_POST_LOAD macro or variable_user_post_load_extension:
# PURGE_LENGTH=[float] (optional) The length to purge. If ommited it will check the 
#                      purge_volumes matrix or variable_purge_length
#PURGE_RET=[float]    (optional) The length to retract between moves
#
[gcode_macro BLOBIFIER]
# These parameters define your filament purging. The retract variable is used to retract 
# right after purging to prevent unnecessary oozing. Some filament are particularly oozy 
# and may continue to ooze out of the nozzle for a second or two after retracting. Update 
# as necessary.
variable_purge_spd:            400	     # Speed, in mm/min, of the purge.
variable_purge_temp_min:       245	     # Minimum nozzle purge temperature.
variable_retract_before_park:    0.0     # gpw - was 1 - amount in mm. 0 to disable
variable_retract_speed:       2000       # mm/m

# Adjust this so that your nozzle scrubs within the brush. Be careful not to go too low! 
# Start out with a high value (like, 6) and go 
# down from there.
#variable_brush_top:             6 

# These parameters define your scrubbing, travel speeds, safe z clearance and how many 
# times you want to wipe. Update as necessary.
variable_clearance_z:           2	         # When traveling, but not cleaning, the 
                                           #   clearance along the z-axis between nozzle 
                                           #   and brush.
#variable_wipe_qty:              2	         # Number of complete (A complete wipe: left, 
                                           #   right, left OR right, left, right) wipes.
variable_travel_spd_xy:     10000	         # Travel (not cleaning) speed along x and 
                                           #   y-axis in mm/min.
variable_travel_spd_z:       1000	         # Travel (not cleaning) speed along z axis 
                                           #   in mm/min.
variable_wipe_spd_xy:       10000	         # Nozzle wipe speed in mm/min.


# These parameters define the size of the brush. Update as necessary. A visual reference 
# is provided below.
# 
#                  ?   brush_width   ?                            
#                   _________________                                                          
#                  |                 |  ?                Y position is acquired from your 
#  brush_start (x) |                 | brush_depth       stepper_y position_max. Adjust 
#                  |_________________|  ?                your brush physically in Y so 
#                          (y)                           that the nozzle scrubs within the 
#                      brush_front                       brush.                                              
# __________________________________________________________
#                     PRINTER FRONT
# 
# 
# Start location of the brush. Defaults for 250, 300 and 350mm are provided below. 
# Uncomment as necessary
#variable_brush_start:          34	# For 250mm build    
#variable_brush_start:           67  # For 300mm build
variable_brush_start:          7  # gpw - revised for my setup - for 350mm build

# width of the brush
#variable_brush_width:          35	

# Location of where to purge. The tray is 15mm in length, so if you assemble it against 
# the side of the bed (default), 10mm is a good location
variable_purge_x: 7

# Height of the tray. If it's below your bed, give this a negative number equal to the 
# difference. If it's above your bed, give it a positive number. You can find this number 
# by homing, optional QGL or equivalent, and moving you toolhead above the tray, and 
# lowering it with the paper method. 
variable_tray_top: 0.0


# ========================================================================================
# ==================== BLOB TUNING =======================================================
# ========================================================================================

# The following section defines how the purging sequence is executed. This is where you 
# tune the purging to create pretty blobs. Refer to the visual reference for a better 
# understanding. The visual is populated with example values. Below are some guides 
# provided to help with tuning.
#
#                          \_____________/
#                             |___|___|
#                                \_/            ______________  < End of third iteration.
#                                / \                                  HEIGHT:   3 x iteration_z_raise - (2 + 1) x iteration_z_change  (3 x 5 - 2 x 1.2 = 11.4)
#                               |   |                                 EXTRUDED: 3 x max_iteration_length                              (3 x 50 = 150)
#                              /     \          ______________  < End of second iteration.
#                             |       \                               HEIGHT:   2 x iteration_z_raise - 1 x iteration_z_change        (2 x 5 - 1 x 1.2 = 8.8)
#                            /         |                              EXTRUDED: 2 x max_iteration_length                              (2 x 50 = 100)
#                           |           \       ______________  < End of first iteration. 
#                          /             \                            HEIGHT:   1 x iteration_z_raise                                 (1 x 5 = 5)
#                         |               |                           EXTRUDED: 1 x max_iteration_length                              (1 x 50 = 50)
#___________               \             /      ______________  < Start height of the nozzle. default value: 1.5mm
#           |_______________\___________/_      ______________  < Bottom of the tray
#           |_____________________________|
#           |
# 
########################### BLOB TUNING ##############################
# +-------------------------------------+----------------------------+
# |  Filament sticks to the nozzle at   | Incr. purge start          |
# |    initial purge (first few mm)     |                            |
# +-------------------------------------+----------------------------+
# |  Filament scoots out from under     | Incr. temperature          |
# |  the nozzle at the first iteration  | Decr. iteration_z_raise    |
# |                                     | Incr. max_iteration_length |
# +-------------------------------------+----------------------------+
# |  Filament scoots out from under the | Decr. purge_spd            |
# |  the nozzle at later iterations     | Incr. iteration_z_change   |
# +-------------------------------------+----------------------------+
# |  Filament sticks to the nozzle at   | Decr. iteration_z_change   |
# |         later iterations            |                            |
# +-------------------------------------+----------------------------+
# |        I think my blobs can         | Balsy... Increase          |
# |          be much bigger!            | max_iterations_per_blob    |
# +-------------------------------------+----------------------------+
#

# The height to raise the nozzle above the tray before purging. This allows any built up 
# pressure to escape before the purge.
variable_purge_start: 0.0  # gpw - was 0.2

# The maximum mm of filament (length) to extrude one iteration. A blob contains multiple 
# iterations
variable_max_iteration_length: 40  # gpw - was 50, 30 was too small/tall - trying to get small blobs taller

# The amount to raise Z for each iteration
variable_iteration_z_raise: 6   #gpw - was 5

# As the nozzle gets higher and the blob wider, the Z raise needs to be reduced.
variable_iteration_z_change: .9  #gpw - was 0.8

# Maximum iterations per blob. 3 Should be sufficient for most flushes. If not, Blobifier 
# will create multiple blobs for a single purge.
variable_max_iterations_per_blob: 3

# Lift the nozzle slightly after creating the blob te release pressure on the tray.
variable_eject_hop: 0.0   # gpw - was 1

# Dwell time (ms) after purging and before cleaning to relieve pressure from the nozzle.
variable_pressure_release_time: 0  #gpw - was 1000

# Set the part cooling fan speed. Disabling can help prevent the nozzle from cooling down 
# and stimulate flow, Enabling it can prevent blobs from sticking together. Values range 
# from 0 .. 1, or -1 if you don't want it changed.
#variable_part_cooling_fan: -1              # Leave it unchanged
#variable_part_cooling_fan:  0              # Disable the fan
variable_part_cooling_fan:  1               # Run it at full speed
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

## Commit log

2024-01-07 version 0.1
    [Base.stl, Blobifier.scad, Servo_arm.stl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]
2024-01-07 added BOM... sort of
2024-01-07 BOM correction
2024-01-07 add another wiggle with the tray
    [blobifier.cfg]
2024-01-08 add bucket and reduce base height
    [Blobifier.scad, Bucket.stl]
2024-01-08 reduce base height
    [Base.stl]
2024-01-08 jst plug
    [Base.stl, Blobifier.scad]
2024-01-08 enlarged bucket and added 250 and 350mm versions
    [Blobifier.scad, Bucket.stl, Bucket_V2-250mm.stl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]
2024-01-08 refined jst connector hole
    [Base.stl, Blobifier.scad]
2024-01-10 Added nozzle nudge and fixed raise_z bug
    [Base.stl, Blobifier.scad, Servo_arm.stl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]
2024-01-10 Forgot to save...
    [blobifier.cfg]
2024-01-14 beefed up the tray
    [Base.stl, Blobifier.scad, Bucket_V2-250mm.stl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]
2024-01-17 version 0.2
    [Base.stl, Blobifier.scad, Tray.stl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]
2024-01-17 Add GIF and edit readme. Also change .cfg a bit
    [blobifier.cfg]
2024-01-17 inluded the brush holder
    [brush_holder_sheet_stop_rev4.stl]
2024-01-18 Add .STEP file
    [Blobifier.scad]
2024-01-18 Add more .STEP files
    [Base.step, Servo_arm.step, Tray.step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]
2024-01-19 Add files for branch
    [21T_servo_arm.SLDPRT, Blobifier.SLDASM, base.SLDPRT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]
2024-01-19 Add support and step files
    [21T_servo_arm.SLDPRT, Blobifier.SLDASM, Blobifier.STEP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]
2024-01-19 learning, bear with me
    [21T_servo_arm.SLDPRT, Blobifier.SLDASM, Blobifier.STEP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]
2024-01-19 Still learning
    [21T_servo_arm.SLDPRT, Blobifier.SLDASM, base_featured.SLDPRT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]
2024-01-19 Update Files
    [Blobifier.step]
2024-01-19 small tweaks
    [21T_servo_arm.SLDPRT, Blobifier.SLDASM, base_featured.SLDPRT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]
2024-01-19 v0.3.0-1 - fixed shaker size
    [Blobifier.scad, Shaker_Arm_SB.stl, Shaker_SB.stl]
2024-01-19 v0.3.0-2 - increased shakeer clearance from base
    [Blobifier.scad]
2024-01-20 v0.3.0-3 - Build guide, shaker size, Servo cable caivity, switch screw hole height for printability
    [Blobifier.scad, Shaker_SB.stl]
2024-01-20 v0.3.0-4 add macro's for added features
    [blobifier.cfg]
2024-01-22 Updated the config with the shaker modules
    [blobifier.cfg]
2024-01-22 renewed .step files
    [Base.step, Blobifier.FCStd, Brush.step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]
2024-01-23 Add step file from Fusion360
    [Base.step, Blobifier.scad, Brush.step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]
2024-01-24 First version done
    [Base.stl, Brush.stl, Bucket_V2-250mm.stl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]
2024-01-24 Added Chamfers
    [SB_Shaker.stl, SB_Shaker_arm.stl]
2024-01-24 Add supports and 250/350 buckets
    [Bucket_V2.4-250.stl, Bucket_V2.4-300.stl, Bucket_V2.4-350.stl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]
2024-01-24 v1.0.1-0 Update renders and remove old files
    [Blobifier.scad, blobifier.cfg]
2024-01-24 v1.0.2-0 restored brush .stl
    [21T_servo_arm.SLDPRT, Blobifier.SLDASM, Blobifier.step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]
2024-01-25 v1.0.3-0 Fixed some tolerance issues
    [Base.stl, Mount_voron_2.4.stl, Tray.stl]
2024-01-25 v1.0.3-1 If the temperature is already set but not reached, the macro will wait instead of setting purge_temp_min
    [blobifier.cfg]
2024-01-25 V1.0.4 Disable part cooling fan during the Blobifier macro
    [blobifier.cfg]
2024-01-25 v1.0.4-1 Small error in cfg. Don't tell anyone
    [blobifier.cfg]
2024-01-25 v1.0.4-2 Oriented parts
    [Base.stl, Blobifier.step, Bucket_V2.4-250.stl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]
2024-01-25 v1.0.4-3 brim height error fixed
    [Blobifier.step, Bucket_V2.4-250.stl, Bucket_V2.4-300.stl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]
2024-01-25 v1.0.5-0 Angled the v2.4 mount a bit down so it sits flush with the bottom
    [Blobifier.step, Mount_voron_2.4.stl]
2024-01-25 v1.0.5-1 Added a step in the assembly proces for cutting the servo arm to length
2024-01-26 v1.0.5-2 Made the part-cooling fan disable an option
    [blobifier.cfg]
2024-01-28 v1.0.5-3 Fixed config alignment
    [blobifier.cfg]
2024-01-29 v1.0.5-5 Recoverd servo arm STL's
    [Servo_arm_L.stl, Servo_arm_M.stl, Servo_arm_S.stl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]
2024-02-02 v1.0.5-6 Small fix for switch lever
    [Base.stl, Blobifier.step]
2024-02-03 v1.0.6-0 Add a higher base version to accomodate the kinematic bed mounts
    [Base_kinematic_bed_mounts.stl]
2024-02-17 v1.1.0-0 Now fits an MG90 servo!
    [Base.stl, Servo_Arm.stl, Servo_arm_L.stl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]
2024-02-19 v1.1.1-0 Add servo up command for use with Happy Hare
    [blobifier.cfg]
2024-02-19 Update blobifier.cfg
    Fix indenting for jinja2 in `blobifier.cfg`
    [blobifier.cfg]
2024-02-20 Add a mount for the slightly wider beds
    [Mount_voron_2.4_5mm_wider_beds.stl]
2024-02-25 v1.2.0-0 More integration with Happy Hare!
    [blobifier.cfg]
2024-02-25 v1.2.1-0 Add xx5mm buckets
    [Bucket_V2.4-255.stl, Bucket_V2.4-305.stl, Bucket_V2.4-355.stl]
2024-02-26 Update blobifier.cfg
    Added SAVE_VARIABLES
    [blobifier.cfg]
2024-02-28 Revised the config file for readability
    [blobifier.cfg]
2024-02-28 streamlined the persistent state
    [blobifier.cfg]
2024-03-01 v1.2.2-0 Fix max purge_volume, streamline output, add purge_minimum
    [blobifier.cfg]
2024-03-05 Add a BLOBIFIER_PARK macro to pre-position the toolhead
    [blobifier.cfg]
2024-03-07 bugfix, organized .stl files, add files for higher beds
    [Base.stl, Base_high_beds.stl, Base_kinematic_bed_mounts.stl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]
2024-03-12 Add files via upload
    Macro for SW only Blobifier on a Voron Trident
    [SW Only Blobifier.cfg]
2024-03-13 v1.3.0-1 Add more base heights
    [Base+1.stl, Base+2.stl, Base+3.stl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]
2024-03-22 remove config file, use HH version
    [SW Only Blobifier.cfg, blobifier.cfg]
2024-07-10 Add shim for universal bed heights
    [Base+1.stl, Base+2.stl, Base+3.stl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]
2024-08-13 v1.4 refine BOM
2025-02-26 A4T Shaker arm user mod
    [Shaker_A4T.step, Shaker_A4T.stl, Shaker_Arm_A4T.step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]
2025-03-16 Shaker arm refinements
    [Shaker_A4T.step, Shaker_Arm_A4T.stl]
